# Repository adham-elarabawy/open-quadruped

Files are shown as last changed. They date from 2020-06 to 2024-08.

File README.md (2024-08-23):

# open-quadruped

PR (https://github.com/adham-elarabawy/OpenQuadruped/pulls)



An open-source 3D-printed quadrupedal robot. Intuitive gait generation through 12-DOF Bezier Curves. Full 6-axis body pose manipulation. Custom 3DOF Leg Inverse Kinematics Model accounting for offsets.

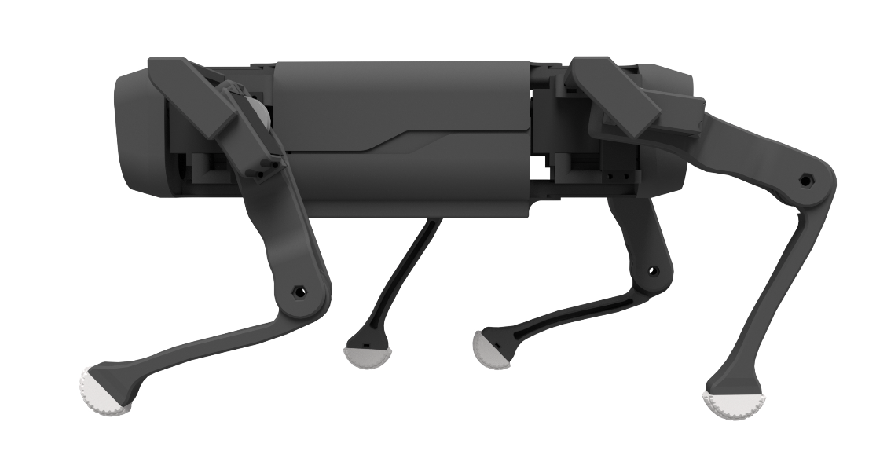
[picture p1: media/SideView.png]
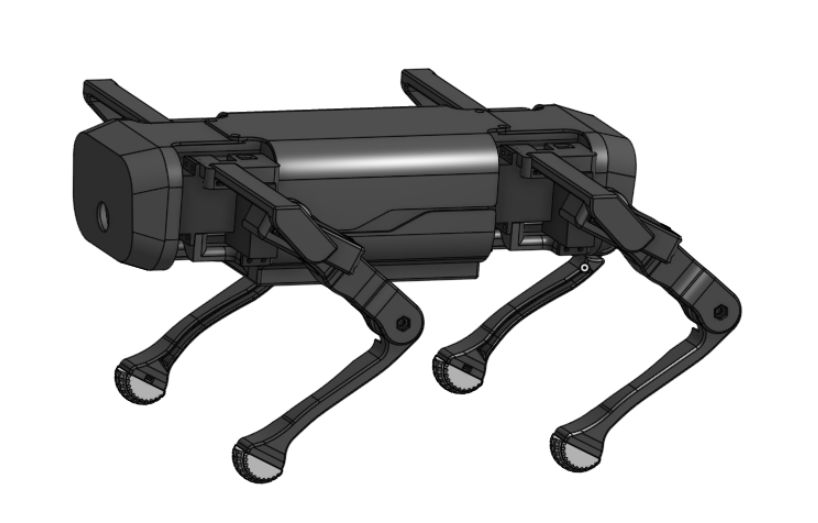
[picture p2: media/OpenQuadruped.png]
 

## Current Status
### To-Do List

- [x] *Hardware* // Redesign legs to move actuators closer to hip + reinforce all servo mounting.
- [ ] *Design* // Research transition between gait & body pose.
- [x] *Software* // Implementing ROS infrastructure for all control processes (including cpp on teensy).
- [ ] *Software* // Write & automate pytest unit tests.
- [ ] *Software* // Integrate unit tests with github actions.
- [x] *Simulation* // Create URDF model. (or port collaborater's URDF: Maurice Rahme)
- [x] *Simulation* // Gazebo
- [ ] *Simulation* // RViz Realtime Model
- [ ] *Design* // Solve offset 3DOF IK model for right limbs _OR_ validate that mirroring angles works for left/right legs
- [ ] *Simulation* // Implement WebGazebo clientside support for non-linux users
- [ ] *Sim-to-Real* // Joint servo calibration
- [ ] *Sim-to-Real* // Refining gait parameters
- [ ] *Simulation* // Reinforcement learning via ARS
- [ ] *Software* // Raibert Huerestic for converting desired velocities into gait parameters
- [ ] *Software* // ROS Nav Stack Layer

  

## Papers
I've been formally documenting this project in the form of papers. You can find them here: [adhamelarabawy.com/images/IK_Model.pdf](https://www.adhamelarabawy.com/images/IK_Model.pdf)

## Documentation
You can find a summary of this project on [my portfolio website's project page](https://www.adhamelarabawy.com).
I'm hosting most of the technical documentation for this project on [this repo's wiki](https://github.com/adham-elarabawy/OpenQuadruped/wiki).

## 3D Model
In the [model](https://github.com/adham-elarabawy/OpenQuadruped/tree/master/model) folder, you can find all of the step & stl files that I used for my build of OpenQuadruped. There, you can also find a Bill of Materials, and some guides (in progress). 

## Hardware
I made a custom pcb board to control the position and speed of 12 servos simultaneously, as well as interface with all of the sensors.

You can find the gerber files for the custom pcb in the [hardware folder](https://github.com/adham-elarabawy/OpenQuadruped/tree/master/hardware) in this repository.

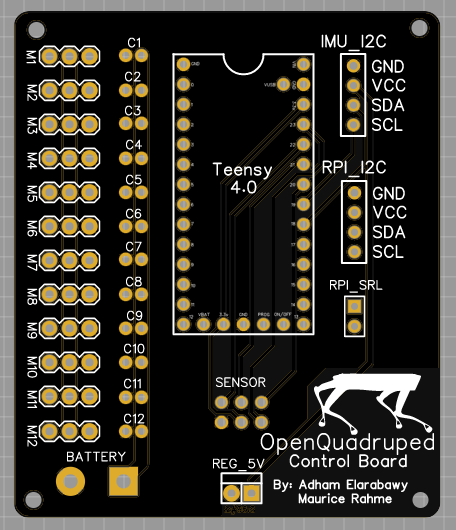
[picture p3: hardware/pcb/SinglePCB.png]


You can find the bill of materials for this project [here](https://docs.google.com/spreadsheets/d/12QX1ca9LHZEThukprlz0DARR9_lmf6FJI8Tg-O4qcdc/edit?usp=sharing).

## Visualization Usage
*NOTE: There are 3 different visualization tools: Gazebo Simulator (ROS + Physics), RViz (ROS), & my custom 3d-matplotlib visualization tool (body IK model + leg IK model). The latter tool is still under development, and I haven't ported it to use my new control library yet, so it is likely broken for the time being.*

To try the visualization tool out, you'll need to run the [animate.py](https://github.com/adham-elarabawy/OpenQuadruped/blob/master/visualization/animate.py) python file with the proper libraries installed. (matplotlib 3.0.3 supported).

You can then use keyboard controls: use x, y, z, a, p, r to select (x axis, y axis, z axis, yaw, pitch, roll), and then the up and down buttons to increment the selected position. If you click '1' on your keyboard, it will reset the position. 

Right now, if you try to go to an impossible pose that would result in collisions, the body will do some weird things. If that happens, just click "1" on your keyboard to reset the position. 

*Note: Pitch and Roll are currently not working. I am currently trying to fix that.*

## More Demos
Force Sensitive Leg Test (https://www.youtube.com/watch?v=z8j-Z9Bwn58)IK Model Demo 0 (https://www.youtube.com/watch?v=79kFujIpjgo)IK Model Demo 1 (https://www.youtube.com/watch?v=cCMvCH0m9TA)IK Model Visualization (https://www.youtube.com/watch?v=LBjqJVEXwhM)

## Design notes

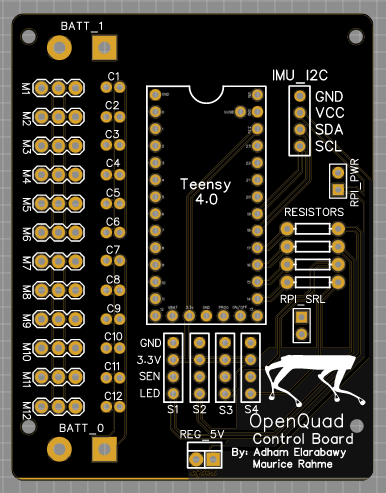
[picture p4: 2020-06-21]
hardware/pcb/DoublePCB.png

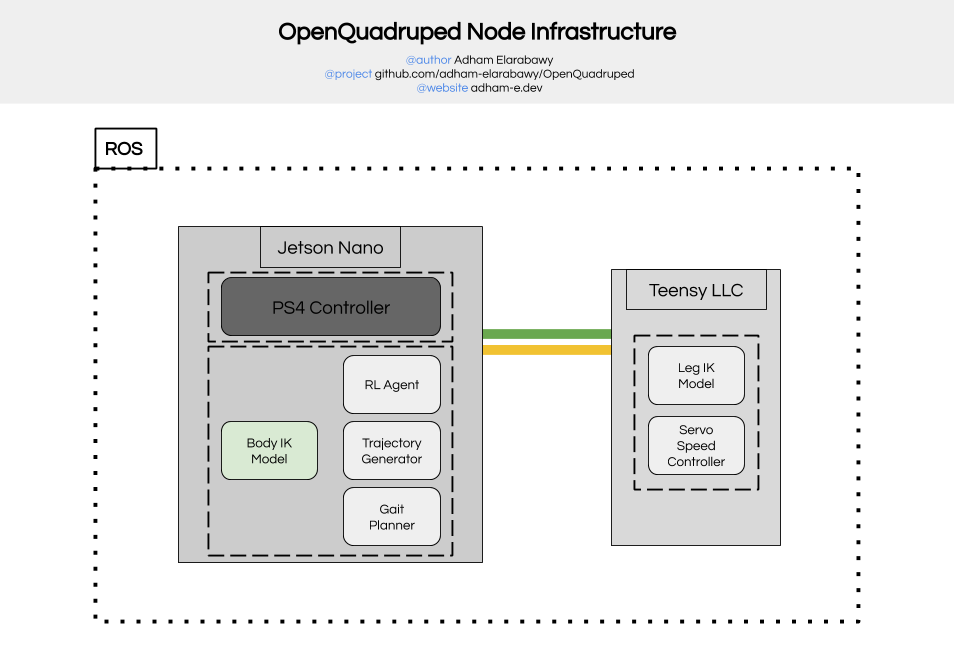
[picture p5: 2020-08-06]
media/OpenQuadruped Node Infrastructure.png

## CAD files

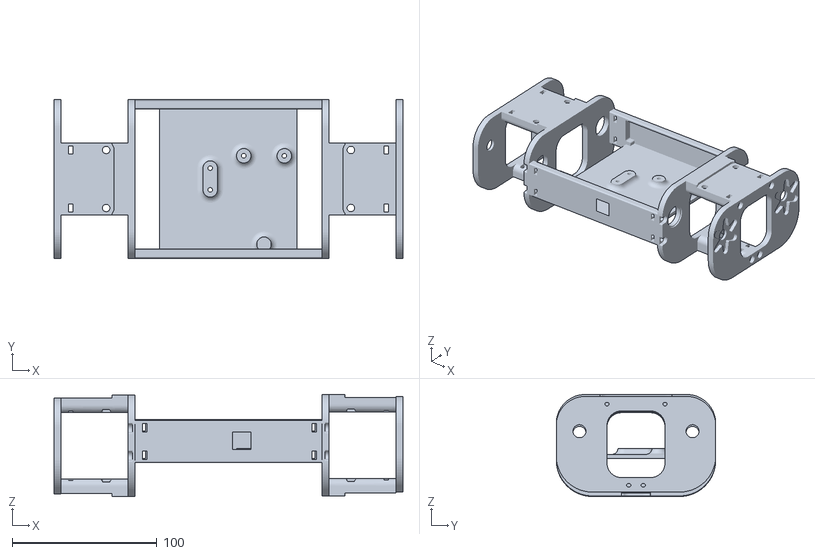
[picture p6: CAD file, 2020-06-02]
ros-workspace/src/open_quadruped/urdf/stl/mainbody.stl
240.7 x 110.0 x 70.4

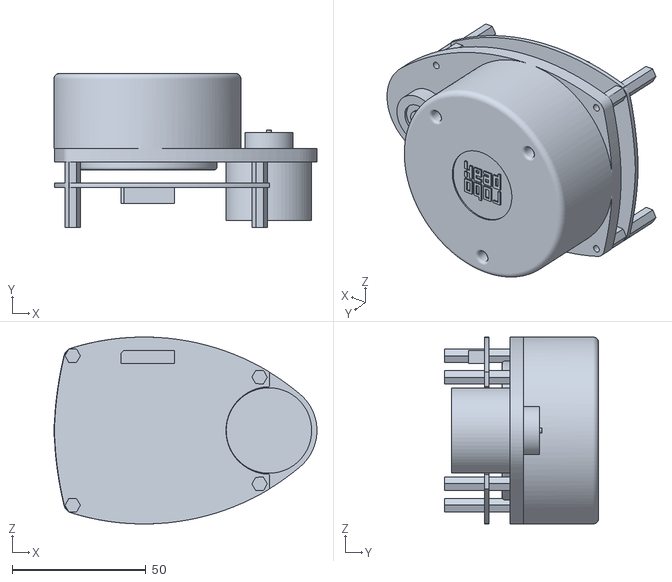
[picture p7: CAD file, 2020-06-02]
ros-workspace/src/open_quadruped/urdf/stl/rplidar_main.stl
98.5 x 57.7 x 70.0

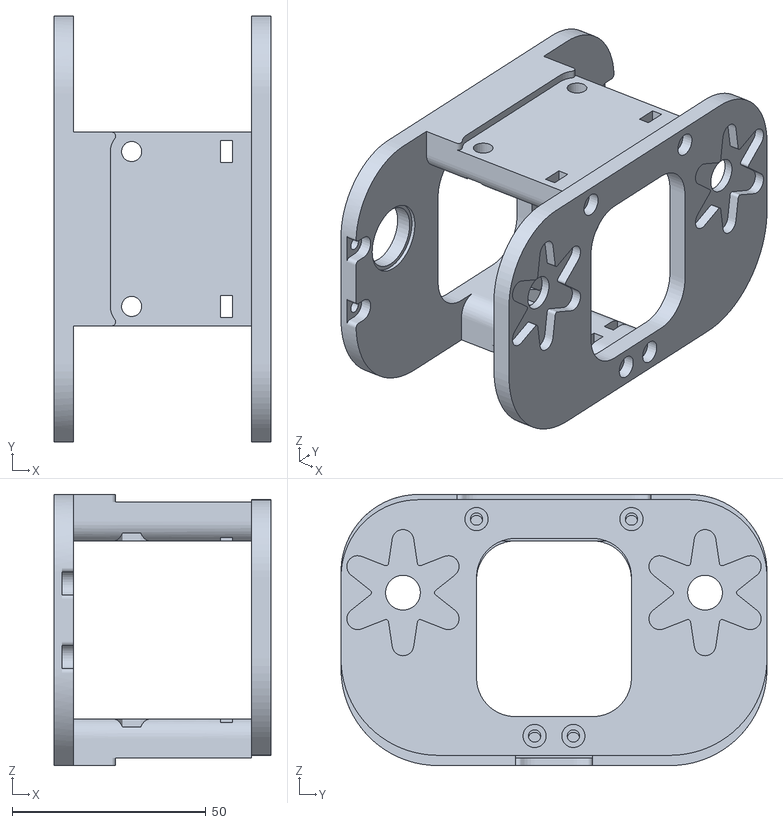
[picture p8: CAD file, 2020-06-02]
ros-workspace/src/open_quadruped/urdf/stl/rearmain.stl
55.9 x 110.0 x 70.0

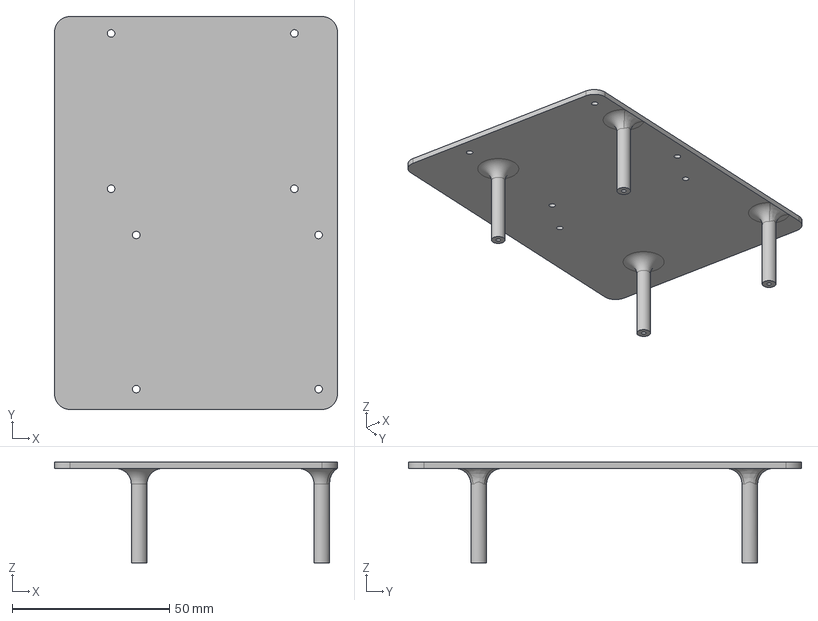
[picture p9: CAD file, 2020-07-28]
hardware/3d-printing/Body/step/Adapter_Plate.step
90.0 x 125.0 x 32.0 mm

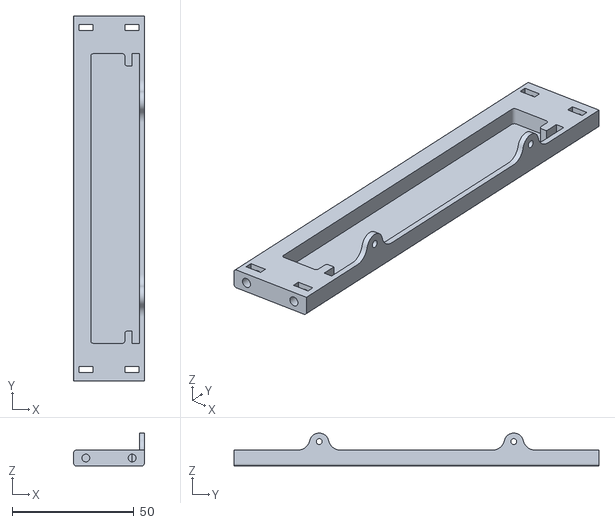
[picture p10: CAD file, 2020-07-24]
hardware/3d-printing/Body/stl/Chassis_Right_Side.stl
29.0 x 150.0 x 13.5

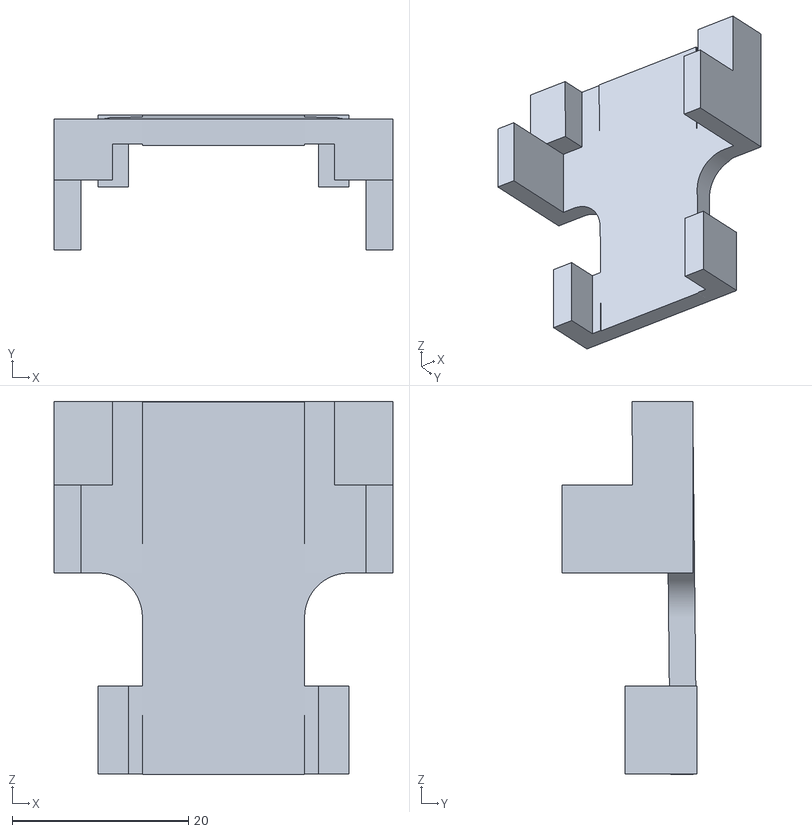
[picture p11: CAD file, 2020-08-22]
hardware/3d-printing/Calibration/Lower_Leg_Calibrator.stl
38.4 x 15.2 x 42.3

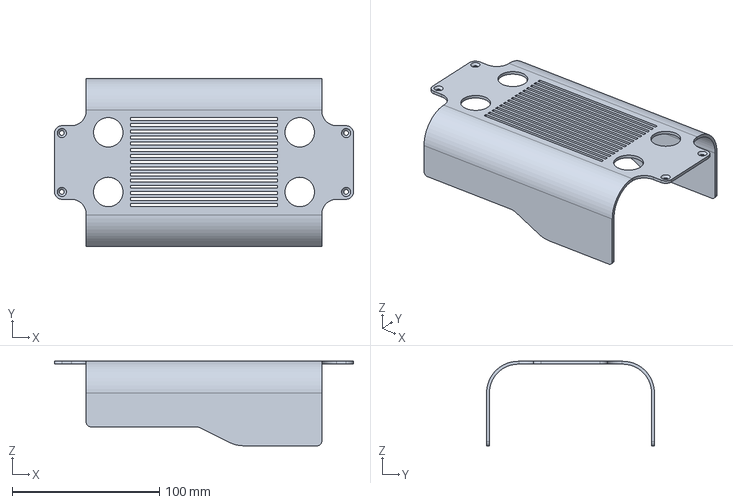
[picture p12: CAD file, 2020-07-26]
hardware/3d-printing/Covers/step/Top.step
203.0 x 114.0 x 57.4 mm

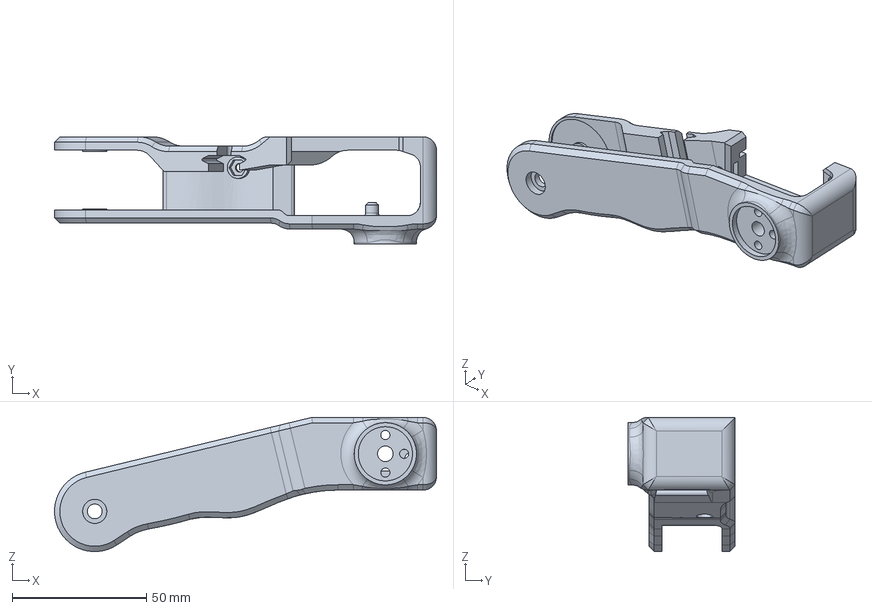
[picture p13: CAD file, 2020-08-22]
hardware/3d-printing/Legs/Left/step/Upper_Leg.step
142.3 x 40.0 x 50.0 mm

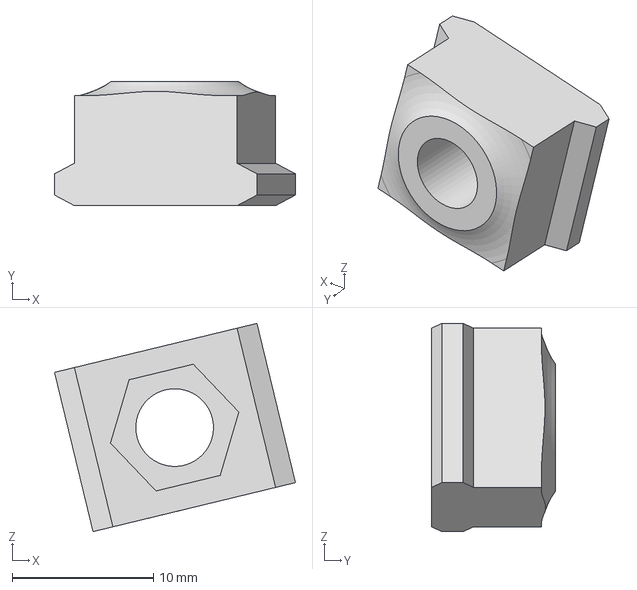
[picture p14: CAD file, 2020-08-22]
hardware/3d-printing/Legs/Right/step/Idler_Mount.step
17.1 x 8.80 x 14.7 mm

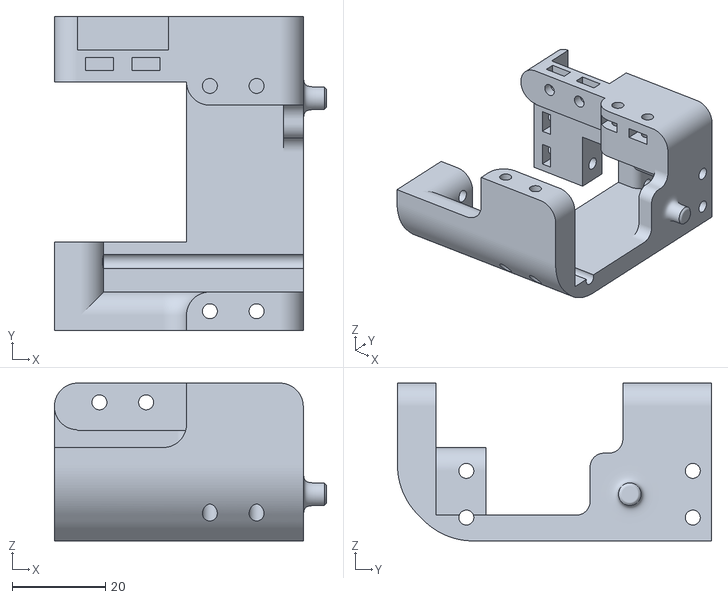
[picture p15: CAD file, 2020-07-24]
model/Legs/Left/stl/Left_Hip_Joint.stl
58.3 x 67.2 x 33.8

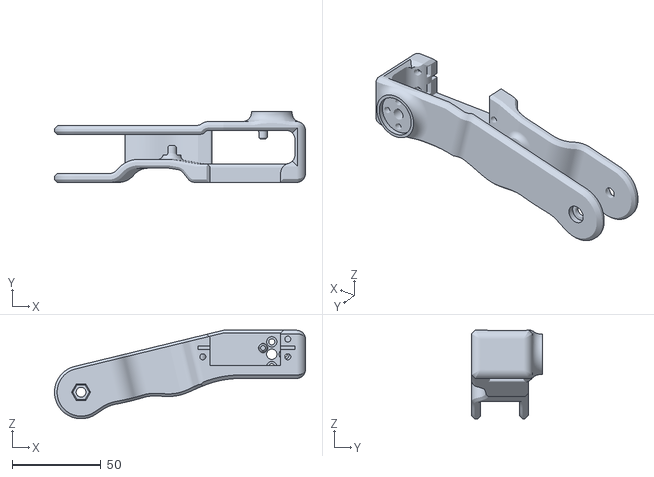
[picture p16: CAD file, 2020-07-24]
model/Legs/Right/stl/Upper_Leg.stl
141.8 x 40.0 x 50.0

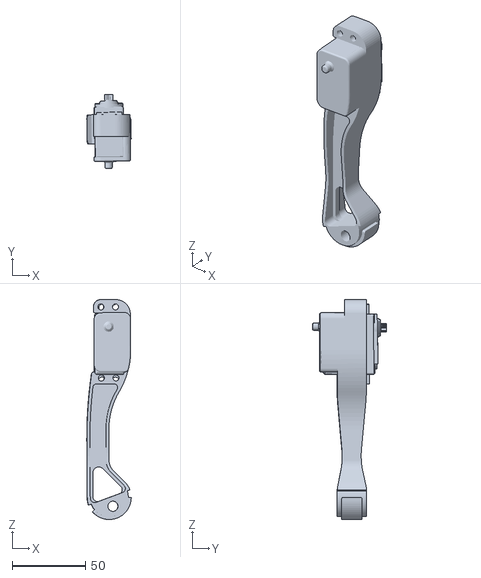
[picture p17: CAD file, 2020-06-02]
ros-workspace/src/open_quadruped/urdf/stl/lfoot.stl
30.4 x 50.7 x 150.0

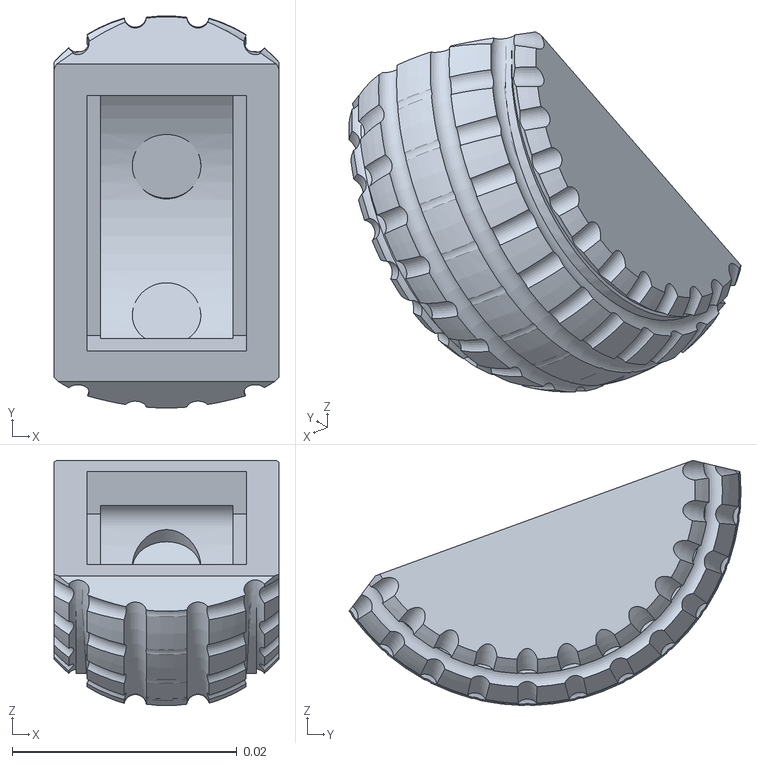
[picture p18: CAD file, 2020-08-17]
ros-workspace/src/open_quadruped/urdf/stl/OpenQuadruped/RIGHT_FOOT.stl
0.02 x 0.0349 x 0.0218

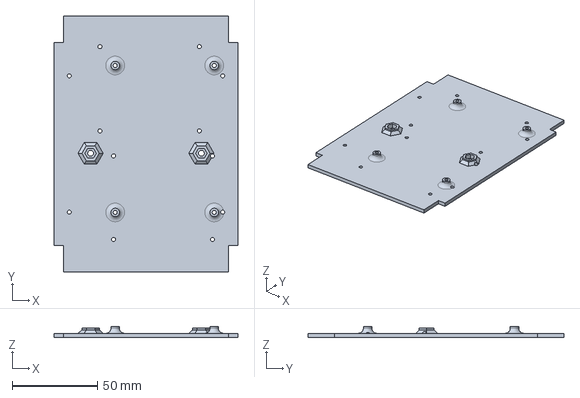
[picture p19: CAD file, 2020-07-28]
hardware/3d-printing/Body/step/Electronics_Plate.step
108.0 x 149.9 x 6.50 mm

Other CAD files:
hardware/3d-printing/Calibration/Hip_Calibrator.stl
hardware/3d-printing/Covers/step/Rear.step
hardware/3d-printing/Legs/Left/step/Idler_Mount.step
hardware/3d-printing/Legs/Right/step/Upper_Leg.step
hardware/3d-printing/Body/step/Back_Inner_Shoulder.step
hardware/3d-printing/Body/step/Back_Outer_Shoulder.step
hardware/3d-printing/Body/step/Chassis_Left_Side - Chassis_Right_Side.step
hardware/3d-printing/Body/step/Chassis_Left_Side.step
hardware/3d-printing/Body/step/Front_Inner_Shoulder.step
hardware/3d-printing/Body/step/Front_Outer_Shoulder.step
hardware/3d-printing/Body/stl/Adapter_Plate.stl
hardware/3d-printing/Body/stl/Back_Inner_Shoulder.stl
hardware/3d-printing/Body/stl/Back_Outer_Shoulder.stl
hardware/3d-printing/Body/stl/Electronics_Plate.stl
hardware/3d-printing/Body/stl/Front_Inner_Shoulder.stl
hardware/3d-printing/Body/stl/Front_Outer_Shoulder.stl
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

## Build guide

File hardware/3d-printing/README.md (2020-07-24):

# 3D Model
In this folder, you can find all of the modified step & stl files that I used for my build of OpenQuadruped.

## Instructions
In Progress...

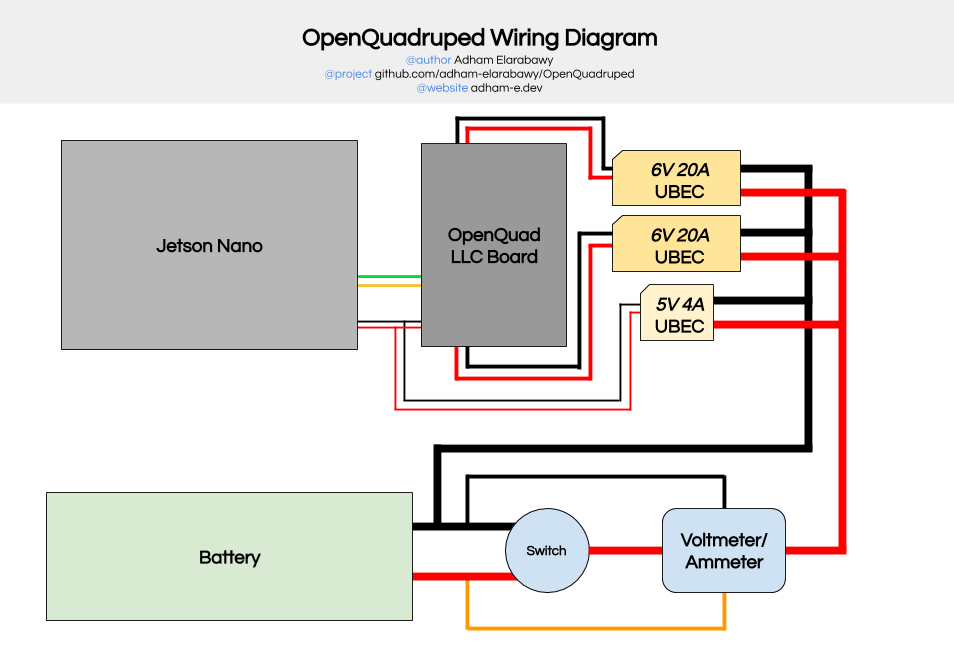
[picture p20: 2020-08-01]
media/wiring_diagram.png

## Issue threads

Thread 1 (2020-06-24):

Servo Detach() function

mano1979, 2020-06-24:
I wondered if you could add a function like this to the servo control code. It is to detach the servos and thus make them loose power. This is handy for shutting the robot down in an emergency for example. i am not familiar enough with your code yet so i can not implement it myself.

Here is the piece of code from the normal arduino Servo.cpp:

`void Servo::detach()
{
  servos[this->servoIndex].Pin.isActive = false;
  timer16_Sequence_t timer = SERVO_INDEX_TO_TIMER(servoIndex);
  if(isTimerActive(timer) == false) {
    finISR(timer);
  }
}`

adham-elarabawy, 2020-06-24:
Great Idea! I will put this on the to-do list.

mano1979, 2020-06-25:
Also, is this teensy code complete? I cannot find any pin definitions anywhere. Where do you tell it to use the GPIO 2-12 for the servos?

adham-elarabawy, 2020-06-30:
I haven't properly documented everything yet. The plan is to do that sometime this week.

I tried to servo.detach() that you mentioned, but it doesn't really release the servos in the way that I expected. Most servos hold their positions when you detach them, not actually release servo power. This behavior is equivalent to my estop functionality on the teensy, which halts all the servos as soon as 'e' or 'E' is sent over serial, so I think servo.detach is redundant.

mano1979, 2020-07-07:
I found this topic online that explains why it doesn't work and a possible workaround. it seems the timers on the teensy aren't reset when a servo is detached, keeping the PWM signal alive ( if i understood right).

https://github.com/arduino/Arduino/issues/3860

adham-elarabawy, 2020-07-11:
I'll take a look.

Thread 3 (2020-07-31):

Integrating with ROS

adham-elarabawy, 2020-07-31:
In order to switch to using a ROS infrastructure, there needs to be significant work done on refactoring much of the codebase. It is as follows:
 - [x] Jetson Nano Networking setup
   - [x] autoconnect to laptop's network
   - [x] document connection procedure
 - [x] Install ROS melodic on Jetson Nano
 - [ ] Verify ROS functionality
   - [x] sub & pub to topics using nodes on jetson nano
   - [x] serial comm between jetson nano / teensy
   - [x] sub & pub to topics using nodes on jetson nano / teensy
   - [ ] ~sub & pub to topics using nodes on teensy~
     - Not possible. Teensy can only act as 1 node.
 - [x] Based on the results of above task, determine proper node layout
   - [x] create diagram (https://github.com/adham-elarabawy/OpenQuadruped/wiki/ROS-Node-Infrastructure)
 - [ ] Refactor codebase
   - [x] Import ros libs in teensy lib dir
   - [x] Implement base ROS init + callback in teensy
   - [x] Test ros joy lib with ds4drv ps4 driver
   - [x] Create custom message for 4 leg poses
   - [x] Header files for custom message on teensy
   - [x] Experiment with ROS ps4 controller packages
   - [x] Minor refactoring for main jetson nano control process. Node-ify it.
   - [ ] Modify LLC c++ code to remove Leg IK from teensy (LLC should accept joint angles, not leg htf vectors).

adham-elarabawy, 2020-08-01:
All references to "documentation" are referring to the repo wiki.

caelinsutch, 2020-08-06:
Are you planning on integrating sim?

adham-elarabawy, 2020-08-06:
Yes, but I'm not sure if I'm going to use Gazebo or pybullet

adham-elarabawy, 2020-08-06:
I'd like to finish base ROS integration first, then write some unit tests for some of the inverse kinematics classes. Then, sim -> RL.

adham-elarabawy, 2020-08-06:
Created ROS Node Infrastructure diagram + explanation of control processes. https://github.com/adham-elarabawy/OpenQuadruped/wiki/ROS-Node-Infrastructure

caelinsutch, 2020-08-06:
> Created ROS Node Infrastructure diagram + explanation of control processes. https://github.com/adham-elarabawy/OpenQuadruped/wiki/ROS-Node-Infrastructure

You didn't link anything

adham-elarabawy, 2020-08-06:
> > Created ROS Node Infrastructure diagram + explanation of control processes. https://github.com/adham-elarabawy/OpenQuadruped/wiki/ROS-Node-Infrastructure
>
> You didn't link anything

Hm, on my end it looks like I linked the documentation in the comment you replied to + in the checklist. Is that not showing up for you?

caelinsutch, 2020-08-06:
@adham-elarabawy Mobile redirected me to the home page, on my desktop it's showing up fine!

caelinsutch, 2020-08-19:
The package configuration is still pretty non standard, take a look at [this repo](https://github.com/chvmp/champ)

Closed 2020-08-17.

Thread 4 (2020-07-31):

Inverse Kinematics Model revision

adham-elarabawy, 2020-07-31:
After using the IK model I created & documented, I have noticed some flaws with my implementation. I'd like to try out a couple of new things:
 - [ ] Error catching
   - [ ] Out of bounds
   - [ ] Ability to set custom limits on arm angles based on hardware restrictions
 - [ ] Use right hand rule model consistently
 - [ ] Update documentation

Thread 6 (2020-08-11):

About the pulleys on the 3D model

takanotume24, 2020-08-11:
Hi, I'm from the spot_mini_mini repository.
I saw the video on Youtube, and I think it's a great robot, so I'd love to make one myself!

Viewed on https://cad.onshape.com/documents/9d0f96878c54300abf1157ac/w/c9cdf8daa98d8a0d7d50c8d3/e/fa0d7caf0ed2ef46834ecc24, Did you make the pulleys with a 3D printer?
Or do you use a commercial product?

adham-elarabawy, 2020-08-11:
The pulleys (like 90% of the parts on the quadruped) are 3D printed. They're made to fit 300mm 2GT belts. Please let me know if you have any other questions.

Closed 2020-08-11.

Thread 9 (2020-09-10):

Assembly specifically belt tensioner

wiltonburke, 2020-09-10:
Do you have any documents or guides on assembly. I'm not sure exactly how you did the belt tension. Also the alignment of the servos would also be helpful. If not guides them possibly some pictures.

Thank You.

wiltonburke, 2020-09-10:
This is what I have so far. It looks like it would bind or wear out poorly against the side of leg.

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

adham-elarabawy, 2020-09-10:
Hi @wiltonburke. I'm currently a bit busy with my undergraduate workload, but I can try and guide you through the assembly. From the picture, it looks like the belt is slipped off of the bearing. The ideal behavior is that the belt lies flat against the idler bearing. Please try reorienting it and let me know if that solves your problem.

wiltonburke, 2020-09-10:
I may adjust the design to use something like https://www.thingiverse.com/thing:24661

On the alignment of the servos I can see it doesn't matter much on the belt thats pretty adjustable to fix by sliding the belt. But the alignment on the 2 shoulder servos. What do you recommend?

adham-elarabawy, 2020-09-11:
By alignment of the shoulder servos, do you mean the range of the servo? Or are you referencing mechanical alignment? There should only be one way to mount the shoulder servos.

wiltonburke, 2020-09-11:
I mean the range of the servos. Where do you place the min and the max. The servos usually provide 180 degrees of motion. I don't know how much experimentation you have done, but I'm asking because I noticed when I put the leg together the first time I placed it where it would have very little motion stepping forward. The 2 servos in the shoulder are a little harder to adjust then the belt drive to the lower leg so I'd like to get them aligned correctly before building the other 3 legs. I'll have to rebuild the first leg anyways because I order some 35kg servos to replace the mixture I have now.

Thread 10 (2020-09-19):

initial pose at boot needed for servos placement !!

elpimous, 2020-09-19:
Hey, Adham, working on your package, and need to know what alignement servos need to be at teensy boot !!
Could you quickly tell me their position :
- Hips right, and parallel to ground ?
- shoulders // to others shoulders, and perpendicular to ground ?
- wrist        // to others wrists, and perpendicular to ground ?
Thanks in avance, Adham
Vincent

domcross, 2021-01-02:
There is a calibration mode that sets servos to aligned positions, see calibration guide for details: https://github.com/OpenQuadruped/spot_mini_mini/blob/spot/spot_real/Calibration.md

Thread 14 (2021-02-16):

Parts list link no longer working

ARingshall, 2021-02-16:
Hi Adham
great project, just wondering if you have the parts list still available as it appears to have been deleted?

Cheers
Alex

domcross, 2021-02-17:
see link "BOM" here: https://github.com/OpenQuadruped/spot_mini_mini/tree/spot/spot_real

or direct link: https://docs.google.com/spreadsheets/d/1Z4y59K8bY3r_442I70xe564zAFuP0pVIFEJ6bNZaCi0/edit?usp=sharing

ARingshall, 2021-02-19:
Nice one, cheers mate

Closed 2021-02-19.

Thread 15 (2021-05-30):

Idler stl missing

rachaelsmith423, 2021-05-30:
I see in both the leg folders, there is a idler mount stl. I also see in the CAD model that there is an idler. Yet, I don't see where the actual idler's stl file. Would you please mind uploading this? I assembled the rest, but tensioning the belt would definitely make the legs move better. Thank you

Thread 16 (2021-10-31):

Broken bill of materials link - says that the file was deleted

Milind220, 2021-10-31:

domcross, 2021-10-31:
The link to the BOM was most likely deleted because Adhams repo is outdated - I would recommend to use the new repo instead:
https://github.com/OpenQuadruped/spot_mini_mini

Link to latest BOM can be found there as well (in section [spot_real](https://github.com/OpenQuadruped/spot_mini_mini/tree/spot/spot_real)): https://docs.google.com/spreadsheets/d/1Z4y59K8bY3r_442I70xe564zAFuP0pVIFEJ6bNZaCi0/edit?usp=sharing

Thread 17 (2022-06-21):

animate.py roll pitch yaw

haxord7hasib, 2022-06-21:
roll pitch way is not working on animate.py. Is there any update available?

Closed 2022-06-21.

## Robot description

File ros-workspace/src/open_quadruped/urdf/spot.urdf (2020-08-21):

<?xml version="1.0" encoding="utf-8"?>
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
<robot name="spot">
  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
  <link name="base_link"/>
  <link name="base_inertia">
    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
    <inertial>
      <mass value="0.6"/>
      <origin rpy="0 0 0" xyz="0 0 0"/>
      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
    </inertial>
  </link>
  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
  <link name="battery">
    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
    <inertial>
      <mass value="0.4"/>
      <origin rpy="0 0 0" xyz="0 0 0"/>
      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
    </inertial>
  </link>
  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
  <link name="chassis_left">
    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
    <inertial>
      <mass value="0.01"/>
      <origin rpy="0 0 0" xyz="0 0 0"/>
      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
    </inertial>
  </link>
  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
  <link name="chassis_right">
    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
    <inertial>
      <mass value="0.01"/>
      <origin rpy="0 0 0" xyz="0 0 0"/>
      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
    </inertial>
  </link>
  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
  <link name="front">
    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
    <inertial>
      <mass value="0.1"/>
      <origin rpy="0 0 0" xyz="0 0 0"/>
      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
    </inertial>
  </link>
  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
  <link name="back">
    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
    <inertial>
      <mass value="0.1"/>
      <origin rpy="0 0 0" xyz="0 0 0"/>
      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
    </inertial>
  </link>
  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
  <link name="front_bracket">
    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
    <inertial>
      <mass value="0.1"/>
      <origin rpy="0 0 0" xyz="0 0 0"/>
      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
    </inertial>
  </link>
  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
  <link name="back_bracket">
    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
    <inertial>
      <mass value="0.1"/>
      <origin rpy="0 0 0" xyz="0 0 0"/>
      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
    </inertial>
  </link>
  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
  <link name="front_left_hip">
    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
    <inertial>
      <mass value="0.2"/>
      <origin rpy="0 0 0" xyz="0 0.075 0"/>
      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
    </inertial>
  </link>
  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
  <joint name="motor_front_left_hip" type="revolute">
    <axis xyz="1 0 0"/>
    <origin rpy="0 0 0" xyz="0.0915 0.0394 0.022"/>
    <parent link="front_bracket"/>
    <child link="front_left_hip"/>
    <limit effort="4.0" lower="-1.04" upper="1.04" velocity="4.0"/>
    <joint_properties damping="0.0" friction="0.0"/>
  </joint>
  <link name="front_left_upper_leg">
    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
    <inertial>
      <mass value="0.13"/>
      <origin rpy="0 0 0" xyz="-0.005 0.0175 -0.055"/>
      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
    </inertial>
  </link>
  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
  <joint name="motor_front_left_upper_leg" type="revolute">
    <axis xyz="0 1 0"/>
    <origin rpy="0 0 0" xyz="0.0015 0.045 -0.0087"/>
    <parent link="front_left_hip"/>
    <child link="front_left_upper_leg"/>
    <limit effort="4.0" lower="-1.57079632679" upper="2.59" velocity="4.0"/>
    <joint_properties damping="0.0" friction="0.0"/>
  </joint>
  <link name="front_left_lower_leg">
    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
    <inertial>
      <mass value="0.05"/>
      <origin rpy="0 0 0" xyz="-0.01 0 -0.06"/>
      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
    </inertial>
  </link>
  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
  <joint name="motor_front_left_lower_leg" type="revolute">
    <axis xyz="0 1 0"/>
    <origin rpy="0 0 0" xyz="-0.005 0.018 -0.109"/>
    <parent link="front_left_upper_leg"/>
    <child link="front_left_lower_leg"/>
    <limit effort="4.0" lower="-2.9" upper="1.57079632679" velocity="4.0"/>
    <joint_properties damping="0.0" friction="0.0"/>
  </joint>
  <link name="front_left_foot">
    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
    <inertial>
      <mass value="0.005"/>
      <origin rpy="0 0 0" xyz="0 0 0"/>
      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
    </inertial>
  </link>
  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
  <joint name="front_left_leg_foot" type="fixed">
    <origin rpy="0 0 0" xyz="0 0 -0.1265"/>
    <parent link="front_left_lower_leg"/>
    <child link="front_left_foot"/>
  </joint>
  <link name="back_left_hip">
    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
    <inertial>
      <mass value="0.2"/>
      <origin rpy="0 0 0" xyz="0 0.075 0"/>
      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
    </inertial>
  </link>
  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
  <joint name="motor_back_left_hip" type="revolute">
    <axis xyz="1 0 0"/>
    <origin rpy="0 0 0" xyz="-0.1365 0.0394 0.022"/>
    <parent link="back_bracket"/>
    <child link="back_left_hip"/>
    <limit effort="4.0" lower="-1.04" upper="1.04" velocity="4.0"/>
    <joint_properties damping="0.0" friction="0.0"/>
  </joint>
  <link name="back_left_upper_leg">
    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
    <inertial>
      <mass value="0.13"/>
      <origin rpy="0 0 0" xyz="-0.005 0.0175 -0.055"/>
      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
    </inertial>
  </link>
  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
  <joint name="motor_back_left_upper_leg" type="revolute">
    <axis xyz="0 1 0"/>
    <origin rpy="0 0 0" xyz="0.0015 0.045 -0.0087"/>
    <parent link="back_left_hip"/>
    <child link="back_left_upper_leg"/>
    <limit effort="4.0" lower="-1.57079632679" upper="2.59" velocity="4.0"/>
    <joint_properties damping="0.0" friction="0.0"/>
  </joint>
  <link name="back_left_lower_leg">
    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
    <inertial>
      <mass value="0.05"/>
      <origin rpy="0 0 0" xyz="-0.01 0 -0.06"/>
      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
    </inertial>
  </link>
  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
  <joint name="motor_back_left_lower_leg" type="revolute">
    <axis xyz="0 1 0"/>
    <origin rpy="0 0 0" xyz="-0.005 0.018 -0.109"/>
    <parent link="back_left_upper_leg"/>
    <child link="back_left_lower_leg"/>
    <limit effort="4.0" lower="-2.9" upper="1.57079632679" velocity="4.0"/>
    <joint_properties damping="0.0" friction="0.0"/>
  </joint>
  <link name="back_left_foot">
    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
    <inertial>
      <mass value="0.005"/>
      <origin rpy="0 0 0" xyz="0 0 0"/>
      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
    </inertial>
  </link>
  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
  <joint name="back_left_leg_foot" type="fixed">
    <origin rpy="0 0 0" xyz="0 0 -0.1265"/>
    <parent link="back_left_lower_leg"/>
    <child link="back_left_foot"/>
  </joint>
  <link name="front_right_hip">
    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
    <inertial>
      <mass value="0.2"/>
      <origin rpy="0 0 0" xyz="0 -0.075 0"/>
      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
    </inertial>
  </link>
  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
  <joint name="motor_front_right_hip" type="revolute">
    <axis xyz="1 0 0"/>
    <origin rpy="0 0 0" xyz="0.0915 -0.0394 0.022"/>
    <parent link="front_bracket"/>
    <child link="front_right_hip"/>
    <limit effort="4.0" lower="-1.04" upper="1.04" velocity="4.0"/>
    <joint_properties damping="0.0" friction="0.0"/>
  </joint>
  <link name="front_right_upper_leg">
    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
    <inertial>
      <mass value="0.13"/>
      <origin rpy="0 0 0" xyz="-0.005 -0.0175 -0.055"/>
      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
    </inertial>
  </link>
  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
  <joint name="motor_front_right_upper_leg" type="revolute">
    <axis xyz="0 1 0"/>
    <origin rpy="0 0 0" xyz="0.0015 -0.045 -0.0087"/>
    <parent link="front_right_hip"/>
    <child link="front_right_upper_leg"/>
    <limit effort="4.0" lower="-1.57079632679" upper="2.59" velocity="4.0"/>
    <joint_properties damping="0.0" friction="0.0"/>
  </joint>
  <link name="front_right_lower_leg">
    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
    <inertial>
      <mass value="0.05"/>
      <origin rpy="0 0 0" xyz="-0.01 0 -0.06"/>
      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
    </inertial>
  </link>
  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
  <joint name="motor_front_right_lower_leg" type="revolute">
    <axis xyz="0 1 0"/>
    <origin rpy="0 0 0" xyz="-0.005 -0.018 -0.109"/>
    <parent link="front_right_upper_leg"/>
    <child link="front_right_lower_leg"/>
    <limit effort="4.0" lower="-2.9" upper="1.57079632679" velocity="4.0"/>
    <joint_properties damping="0.0" friction="0.0"/>
  </joint>
  <link name="front_right_foot">
    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
    <inertial>
      <mass value="0.005"/>
      <origin rpy="0 0 0" xyz="0 0 0"/>
      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
    </inertial>
  </link>
  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
  <joint name="front_right_leg_foot" type="fixed">
    <origin rpy="0 0 0" xyz="0 0 -0.1265"/>
    <parent link="front_right_lower_leg"/>
    <child link="front_right_foot"/>
  </joint>
  <link name="back_right_hip">
    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
    <inertial>
      <mass value="0.2"/>
      <origin rpy="0 0 0" xyz="0 -0.075 0"/>
      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
    </inertial>
  </link>
  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
  <joint name="motor_back_right_hip" type="revolute">
    <axis xyz="1 0 0"/>
    <origin rpy="0 0 0" xyz="-0.1365 -0.0394 0.022"/>
    <parent link="back_bracket"/>
    <child link="back_right_hip"/>
    <limit effort="4.0" lower="-1.04" upper="1.04" velocity="4.0"/>
    <joint_properties damping="0.0" friction="0.0"/>
  </joint>
  <link name="back_right_upper_leg">
    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
    <inertial>
      <mass value="0.13"/>
      <origin rpy="0 0 0" xyz="-0.005 -0.0175 -0.055"/>
      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
    </inertial>
  </link>
  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
  <joint name="motor_back_right_upper_leg" type="revolute">
    <axis xyz="0 1 0"/>
    <origin rpy="0 0 0" xyz="0.0015 -0.045 -0.0087"/>
    <parent link="back_right_hip"/>
    <child link="back_right_upper_leg"/>
    <limit effort="4.0" lower="-1.57079632679" upper="2.59" velocity="4.0"/>
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

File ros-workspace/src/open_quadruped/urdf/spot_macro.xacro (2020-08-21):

<?xml version="1.0" ?>
<robot xmlns:xacro="http://www.ros.org/wiki/xacro">

  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

  <xacro:macro name="rev_joint" params="name type axis_xyz origin_rpy origin_xyz parent child effort velocity damping friction upper lower">
    <joint name="${name}" type="${type}">
      <axis xyz="${axis_xyz}" />
      <origin rpy="${origin_rpy}" xyz="${origin_xyz}" />
      <parent link="${parent}" />
      <child link="${child}" />
      <limit effort="${effort}" velocity="${velocity}" lower="${lower}" upper="${upper}"/>
      <joint_properties damping="${damping}" friction="${friction}" />
    </joint>
  </xacro:macro>

  <xacro:macro name="frame_joint" params="name type origin_rpy origin_xyz parent child">
    <joint name="${name}" type="${type}">
      <origin rpy="${origin_rpy}" xyz="${origin_xyz}" />
      <parent link="${parent}" />
      <child link="${child}" />
    </joint>
  </xacro:macro>

  <xacro:macro name="mesh_link" params="name origin_xyz origin_rpy meshfile meshscale c_xyz matname mass i_xyz i_rpy length width height">
    <link name="${name}">
      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

      <inertial>
        <mass value="${mass}" />
        <origin rpy="${i_rpy}" xyz="${i_xyz}" /> 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
      </inertial>
    </link>
    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
  </xacro:macro>

  <xacro:macro name="mesh_link_sphere" params="name origin_xyz origin_rpy meshfile meshscale c_xyz matname mass i_xyz i_rpy length width height radius">
    <link name="${name}">
      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

      <inertial>
        <mass value="${mass}" />
        <origin rpy="${i_rpy}" xyz="${i_xyz}" /> 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
      </inertial>
    </link>

    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
  </xacro:macro>


  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

</robot>

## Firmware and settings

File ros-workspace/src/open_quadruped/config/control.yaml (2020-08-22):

plen:
  # Publish all joint states -----------------------------------
  joint_state_controller:
    type: joint_state_controller/JointStateController
    publish_rate: 50

  # Position Controllers ---------------------------------------
  j1_pc:
    type: effort_controllers/JointPositionController
    joint: motor_front_left_shoulder
    pid: {p: 4.0, i: 0.001, d: 0.0023}
  j2_pc:
    type: effort_controllers/JointPositionController
    joint: motor_front_left_leg
    pid: {p: 4.0, i: 0.001, d: 0.0023}
  j3_pc:
    type: effort_controllers/JointPositionController
    joint: foot_motor_front_left
    pid: {p: 4.0, i: 0.001, d: 0.0023}
  j4_pc:
    type: effort_controllers/JointPositionController
    joint: motor_front_right_shoulder
    pid: {p: 4.0, i: 0.001, d: 0.0023}
  j5_pc:
    type: effort_controllers/JointPositionController
    joint: motor_front_right_leg
    pid: {p: 4.0, i: 0.001, d: 0.0023}
  j6_pc:
    type: effort_controllers/JointPositionController
    joint: foot_motor_front_right
    pid: {p: 4.0, i: 0.001, d: 0.0023}
  j7_pc:
    type: effort_controllers/JointPositionController
    joint: motor_rear_left_shoulder
    pid: {p: 4.0, i: 0.001, d: 0.0023}
  j8_pc:
    type: effort_controllers/JointPositionController
    joint: motor_rear_left_leg
    pid: {p: 4.0, i: 0.001, d: 0.0023}
  j9_pc:
    type: effort_controllers/JointPositionController
    joint: foot_motor_rear_left
    pid: {p: 4.0, i: 0.001, d: 0.0023}
  j10_pc:
    type: effort_controllers/JointPositionController
    joint: motor_rear_right_shoulder
    pid: {p: 4.0, i: 0.001, d: 0.0023}
  j11_pc:
    type: effort_controllers/JointPositionController
    joint: motor_rear_right_leg
    pid: {p: 4.0, i: 0.001, d: 0.0023}
  j12_pc:
    type: effort_controllers/JointPositionController
    joint: foot_motor_rear_right
    pid: {p: 4.0, i: 0.001, d: 0.0023}

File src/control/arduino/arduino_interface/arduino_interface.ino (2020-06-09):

#include <Servo.h>

class AdvServo {
  private:
  Servo servo;
  double last_actuated;
  double error_threshold = 0.5;
  int control_range = 270;
  double wait_time = 1;
  double off = 0;
  
  public:
  double goal;
  double pos;
  double spd;
  int leg; // 0: Front Left, 1: Front Right, 2: Back Left, 3: Back Right
  int joint; // 0: Hip, 1: Shoulder, 2: Wrist
  void init(int servo_pin, double starting_angle, double off);
  void setType(int tempLegNum, int tempJointNum);
  void setPosition(double tempPos, double tempSpeed);
  int getPosition();
  void update_clk();
};

void AdvServo::init(int servo_pin, double starting_angle, double tempOffset) {
  servo.attach(servo_pin, 500, 2500);
  off = tempOffset;
  pos = starting_angle + off;
  servo.write((starting_angle + off) * 180 / control_range);
  delay(1000);
  last_actuated = millis();
}

void AdvServo::setType(int tempLegNum, int tempJointNum) { 
  leg = tempLegNum;
  joint = tempJointNum;
}

void AdvServo::setPosition(double tempPos, double tempSpeed) {
  tempPos = tempPos + off;
  if(tempPos > control_range) {
//    Serial.println("Attempted to set position out of control range. Capped at max.");
    tempPos = control_range;
  }

  if(tempPos < 0) {
//    Serial.println("Attempted to set position out of control range. Capped at min.");
    tempPos = 0;
  }
  
  goal = tempPos;
  spd = tempSpeed;
}

int AdvServo::getPosition() {
  return static_cast<int>(pos - off);
}

void AdvServo::update_clk() {
  if(millis() - last_actuated > wait_time){
    if(abs(pos - goal) > error_threshold) {
      int dir = 0;
      if(goal - pos > 0) {
        dir = 1;
      } else if(goal - pos < 0) {
        dir = -1;
      }
      pos += dir * wait_time / 1000 * spd;
      servo.write(pos * 180 / control_range);
      last_actuated = millis();
    }
  }
}

String serialResponse = "";
char sz[] = "FL,H,999.9,999.9"; // general structure with max numbers allowed.
bool ESTOPPED = false;


void upper(char* s) {
  for(int i = 0; i < strlen(s); i++){
    s[i] = toupper(s[i]);
  }
}


AdvServo BR_Hip, BR_Shoulder, BR_Wrist, BL_Hip, BL_Shoulder, BL_Wrist, FR_Hip, FR_Shoulder, FR_Wrist, FL_Hip, FL_Shoulder, FL_Wrist;

void update_servos(){
  // HIPS
  FL_Hip.update_clk();
  FR_Hip.update_clk();
  BR_Hip.update_clk();
  BL_Hip.update_clk();

  // SHOULDER
  FL_Shoulder.update_clk();
  FR_Shoulder.update_clk();
  BR_Shoulder.update_clk();
  BL_Shoulder.update_clk();

  // WRIST
  FL_Wrist.update_clk();
  FR_Wrist.update_clk();
  BR_Wrist.update_clk();
  BL_Wrist.update_clk();  
}

double angleConversion(int leg, int joint, double angle) {
  if(joint == 0){
    if(leg == 0 || leg == 1) {
      angle = -angle;
    }
    angle = angle + 135;
  }
  
  if(joint == 1) {
    if(leg == 0 || leg == 2) {
      angle = 90 + angle;
    }
    if(leg == 1 || leg == 3) {
      angle = 180 - angle;
    }
  }
  
  if(joint == 2) {
    double weird_offset = 50;
    if(leg == 0 || leg == 2) {
      angle = angle - weird_offset;
    }
    if(leg == 1 || leg == 3) {
      angle = (270 + weird_offset) - angle;
    }
  }
  return angle;
}

int inverse_angleConversion(int leg, int joint, double angle) {
  if(joint == 0){
    if (leg == 0 || leg == 1) {
      angle = 135 - angle;
    }
    if (leg == 2 || leg == 3) {
      angle = angle - 135;
    }
  }
  
  if(joint == 1) {
    if(leg == 0 || leg == 2) {
      angle = angle - 90;
    }
    if(leg == 1 || leg == 3) {
      angle = 180 - angle;
    }
  }
  
  if(joint == 2) {
    double weird_offset = 50;
    if(leg == 0 || leg == 2) {
      angle = weird_offset + angle;
    }
    if(leg == 1 || leg == 3) {
      angle = (270 + weird_offset) - angle;
    }
  }
  return angle;
}

void setLegJointIDS() {
  // HIPS
  FL_Hip.setType(0, 0);
  FR_Hip.setType(1, 0);
  BL_Hip.setType(2, 0);
  BR_Hip.setType(3, 0);

  //SHOULDERS
  FL_Shoulder.setType(0, 1);
  FR_Shoulder.setType(1, 1);
  BL_Shoulder.setType(2, 1);
  BR_Shoulder.setType(3, 1);

  //WRISTS
  FL_Wrist.setType(0, 2);
  FR_Wrist.setType(1, 2);
  BL_Wrist.setType(2, 2);
  BR_Wrist.setType(3, 2);
  
}

void setup() {
// Serial.begin(38400);
 Serial1.begin(115200); // default: 9600, 19200, 57600
 
  // HIPS
  FL_Hip.init(4, 135, 0);
  FR_Hip.init(11, 135, 0);
  BL_Hip.init(7, 135, 4);
  BR_Hip.init(8, 135, -8);

  //SHOULDERS
  FL_Shoulder.init(2, 180, 0);
  FR_Shoulder.init(13, 90, -11);
  BL_Shoulder.init(5, 180, 4);
  BR_Shoulder.init(10, 90, -4);

  //WRISTS
  FL_Wrist.init(3, 0, 0);
  FR_Wrist.init(12, 270, 0);
  BL_Wrist.init(6, 0, 0);
  BR_Wrist.init(9, 270, 0);

  setLegJointIDS();
}

int loopIndex = 0;

String getPositions() {
  String temp = "";
  String delimiter = ";";

  // HIPS
//  temp = temp + String(inverse_angleConversion(FL_Hip.leg, FL_Hip.joint, FL_Hip.getPosition())) + delimiter;
//  temp = temp + String(inverse_angleConversion(FR_Hip.leg, FR_Hip.joint, FR_Hip.getPosition())) + delimiter;
//  temp = temp + String(inverse_angleConversion(BL_Hip.leg, BL_Hip.joint, BL_Hip.getPosition())) + delimiter;
//  temp = temp + String(inverse_angleConversion(BR_Hip.leg, BR_Hip.joint, BR_Hip.getPosition())) + delimiter;

  // SHOULDERS
//  temp = temp + String(inverse_angleConversion(FL_Shoulder.leg, FL_Shoulder.joint, FL_Shoulder.getPosition())) + delimiter;
//  temp = temp + String(inverse_angleConversion(FR_Shoulder.leg, FR_Shoulder.joint, FR_Shoulder.getPosition())) + delimiter;
//  temp = temp + String(inverse_angleConversion(BL_Shoulder.leg, BL_Shoulder.joint, BL_Shoulder.getPosition())) + delimiter;
//  temp = temp + String(inverse_angleConversion(BR_Shoulder.leg, BR_Shoulder.joint, BR_Shoulder.getPosition())) + delimiter;
//
  // WRISTS
  temp = temp + String(inverse_angleConversion(FL_Wrist.leg, FL_Wrist.joint, FL_Wrist.getPosition())) + delimiter;
  temp = temp + String(inverse_angleConversion(FR_Wrist.leg, FR_Wrist.joint, FR_Wrist.getPosition())) + delimiter;
  temp = temp + String(inverse_angleConversion(BL_Wrist.leg, BL_Wrist.joint, BL_Wrist.getPosition())) + delimiter;
  temp = temp + String(inverse_angleConversion(BR_Wrist.leg, BR_Wrist.joint, BR_Wrist.getPosition())) + delimiter;

  return temp;
  
}

void loop() {
//  Serial1.println("01,02,03,04,05,06,07,08,09,10,11,12"); // sends current servo positions back to RPi for speed interpolation (aka smooth linear movements)
  if(!ESTOPPED){
    update_servos();
  }
  if (Serial1.available()) {
    serialResponse = Serial1.readStringUntil('\r\n');
    // Convert from String Object to String.
    char buf[sizeof(sz)];
    serialResponse.toCharArray(buf, sizeof(buf));
    char *p = buf;
    char *str;
    int index = 0;
    int leg = -1; //0=FL, 1=FR, 2=BL, 3=BR
    int joint = -1; //0=Hip, 1=Shoulder, 2=Wrist
    double angle = -1;
    double spd = -1;
    while ((str = strtok_r(p, ",", &p)) != NULL) { // delimiter is the dash
      if(strcmp(str, "e") == 0 || strcmp(str, "E") == 0) {
        ESTOPPED = true;
//        Serial.println("ESTOPPED! Restart to resume.");
      }
      if(index == 0) {
        upper(str);
        if(strcmp(str, "FL") == 0){
          leg = 0;
        }
        if(strcmp(str, "FR") == 0){
          leg = 1;
        }
        if(strcmp(str, "BL") == 0){
          leg = 2;
        }
        if(strcmp(str, "BR") == 0){
          leg = 3;
        }
      }

      if(index == 1) {
        upper(str);
        if(strcmp(str, "H") == 0){
          joint = 0;
        }
        if(strcmp(str, "S") == 0){
          joint = 1;
        }
        if(strcmp(str, "W") == 0){
          joint = 2;
        }
      }

      if(index == 2) {
        angle = atof(str);
      }

      if(index == 3) {
        spd = atof(str);
      }
      index++;
    }

    //ERROR CHECK
    if(leg == -1 || joint == -1 || angle == -1 || spd == -1){
//      Serial.println("BIG ERROR -- INCOMPLETE DATA");
    }
    angle = angleConversion(leg, joint, angle);
    
    if(leg == 0) {
      if(joint == 0) {
        FL_Hip.setPosition(angle, spd);
      }
      if(joint == 1) {
        FL_Shoulder.setPosition(angle, spd);
      }
      if(joint == 2) {
        FL_Wrist.setPosition(angle, spd);
      }
    }

    if(leg == 1) {
      if(joint == 0) {
        FR_Hip.setPosition(angle, spd);
      }
      if(joint == 1) {
        FR_Shoulder.setPosition(angle, spd);
      }
      if(joint == 2) {
        FR_Wrist.setPosition(angle, spd);
      }
    }

    if(leg == 2) {
      if(joint == 0) {
        BL_Hip.setPosition(angle, spd);
      }
      if(joint == 1) {
        BL_Shoulder.setPosition(angle, spd);
      }
      if(joint == 2) {
        BL_Wrist.setPosition(angle, spd);
      }
    }

    if(leg == 3) {
      if(joint == 0) {
        BR_Hip.setPosition(angle, spd);
      }
      if(joint == 1) {
        BR_Shoulder.setPosition(angle, spd);
      }
      if(joint == 2) {
        BR_Wrist.setPosition(angle, spd);
      }
    }
    
  }
}

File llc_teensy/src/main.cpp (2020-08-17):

#include <Arduino.h>
#include "AdvServo.h"
#include "FootSensor.h"
#include "InverseKinematics.h"
#include "Util.h"
#include <Servo.h>
#include <ros.h>
// TODO: Include the message header file

using namespace std;

String serialResponse = "";
char msg0[] = "0,-999.9,-999.9,-999.9"; // general structure for normal position command
char msg1[] = "0,-999.9,-999.9,-999.9,-999.9,-999.9,-999.9"; // general structure for normal position/speed command
bool ESTOPPED = false;
int max_speed = 500; // deg / sec

ros::NodeHandle nh;
AdvServo BR_Hip, BR_Shoulder, BR_Wrist, BL_Hip, BL_Shoulder, BL_Wrist, FR_Hip, FR_Shoulder, FR_Wrist, FL_Hip, FL_Shoulder, FL_Wrist;
FootSensor FL_sensor, FR_sensor, BL_sensor, BR_sensor;
AdvServo * hips[4] = {&FL_Hip, &FR_Hip, &BL_Hip, &BR_Hip};
AdvServo * shoulders[4] = {&FL_Shoulder, &FR_Shoulder, &BL_Shoulder, &BR_Shoulder};
AdvServo * wrists[4] = {&FL_Wrist, &FR_Wrist, &BL_Wrist, &BR_Wrist};
Util util;
InverseKinematics ik;

void detach_servos() {
  // HIPS
  FL_Hip.detach();
  FR_Hip.detach();
  BR_Hip.detach();
  BL_Hip.detach();

  // SHOULDER
  FL_Shoulder.detach();
  FR_Shoulder.detach();
  BR_Shoulder.detach();
  BL_Shoulder.detach();

  // WRIST
  FL_Wrist.detach();
  FR_Wrist.detach();
  BR_Wrist.detach();
  BL_Wrist.detach();
}

void update_servos(){
  // HIPS
  FL_Hip.update_clk();
  FR_Hip.update_clk();
  BR_Hip.update_clk();
  BL_Hip.update_clk();

  // SHOULDER
  FL_Shoulder.update_clk();
  FR_Shoulder.update_clk();
  BR_Shoulder.update_clk();
  BL_Shoulder.update_clk();

  // WRIST
  FL_Wrist.update_clk();
  FR_Wrist.update_clk();
  BR_Wrist.update_clk();
  BL_Wrist.update_clk();
}

void update_sensors() {
  FL_sensor.update_clk();
  FR_sensor.update_clk();
  BL_sensor.update_clk();
  BR_sensor.update_clk();
}

void setLegJointIDS() {
  // HIPS
  FL_Hip.setType(0, 0);
  FR_Hip.setType(1, 0);
  BL_Hip.setType(2, 0);
  BR_Hip.setType(3, 0);

  //SHOULDERS
  FL_Shoulder.setType(0, 1);
  FR_Shoulder.setType(1, 1);
  BL_Shoulder.setType(2, 1);
  BR_Shoulder.setType(3, 1);

  //WRISTS
  FL_Wrist.setType(0, 2);
  FR_Wrist.setType(1, 2);
  BL_Wrist.setType(2, 2);
  BR_Wrist.setType(3, 2);

}

void callback( const pose_msg::LegPoses& leg_poses){
  Serial.println("complete message");
  double *p;
  p = ik.run(leg, x, y, z);

  double temp_hip = util.toDegrees(*p);

  if(leg == 1 || leg == 2){
    temp_hip *= -1;
  }
  
  double hip_angle = util.angleConversion(leg, 0, temp_hip);
  double shoulder_angle = util.angleConversion(leg, 1, util.toDegrees(*(p+1)));
  double wrist_angle = util.angleConversion(leg, 2, util.toDegrees(*(p+2)));
  
  double h_dist = abs(hip_angle - (*hips[leg]).getPosition());
  double s_dist = abs(shoulder_angle - (*shoulders[leg]).getPosition());
  double w_dist = abs(wrist_angle - (*wrists[leg]).getPosition());

  double scaling_factor = util.max(h_dist, s_dist, w_dist);

  h_dist /= scaling_factor;
  s_dist /= scaling_factor;
  w_dist /= scaling_factor;

  (*hips[leg]).setPosition(hip_angle, max_speed * h_dist);
  (*shoulders[leg]).setPosition(shoulder_angle, max_speed * s_dist);
  (*wrists[leg]).setPosition(wrist_angle, max_speed * w_dist);
}


ros::Subscriber<pose_msg::LegPoses> sub("leg_poses", &callback);

void setup() {
  ik.init(8.7, 59, 107, 130); // hip offset 0, hip_offset 1, shoulder length, wrist length

  // HIPS
  FL_Hip.init(4, 135, -2);
  FR_Hip.init(11, 135, 0);
  BL_Hip.init(7, 135, 0);
  BR_Hip.init(8, 135, -3);

  //SHOULDERS
  FL_Shoulder.init(2, 180, -3);
  FR_Shoulder.init(13, 90, -14);
  BL_Shoulder.init(5, 180, 5); // +
  BR_Shoulder.init(10, 90, 0); // -

  //WRISTS
  FL_Wrist.init(3, 0, 2);
  FR_Wrist.init(12, 270, -2);
  BL_Wrist.init(6, 0, 2);
  BR_Wrist.init(9, 270, -1);

  FL_sensor.init(A9, 17);
  FR_sensor.init(A8, 16);
  BL_sensor.init(A7, 15);
  BR_sensor.init(A6, 14);

  setLegJointIDS();

  delay(1000);

  nh.initNode();
  nh.subscribe(sub);
}

void loop() {
  nh.spinOnce();
  if(!ESTOPPED){
    update_servos();
  } else {
    detach_servos();
  }
  update_sensors();
}

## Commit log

2020-05-16 Changed to mm + calibrated offsets
2020-05-19 Yaw Implementation
2020-06-02 Added trajectory + stl
    [backpart.stl, foot.stl, frontpart.stl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]
2020-06-06 Added arduino interface layer
2020-06-07 Implemented Arduino Servo Controller
    TODO: add 2-way communication so that the arduino can send back sensor values.
2020-06-09 Added yaw + Increased Baud Rate
2020-06-09 Implemented low pass filter -- controller input
2020-06-09 Added Gerber Files
2020-06-10 Switched to CPP PlatformIO IDE
2020-06-16 Moved leg IK to teensy
2020-06-17 Added 3d models
    [FL_BR_Hip.step, Front_Shoulder.step, L_Cover.step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]
2020-06-17 Dir Restructure
    [FL_BR_Hip.step, Front_Shoulder.step, L_Cover.step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]
2020-06-17 Updated model
    [FL_BR_Hip.step, FL_BR_Hip_Joint.step, FL_BR_Hip_Joint.stl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]
2020-06-17 Updated files
    [Left_Cover.step, Left_Cover.stl]
2020-06-17 Added LED to wrist
    [Left_Wrist.step, Left_Wrist.stl]
2020-06-18 Added Foot Sensor Cabling
    [Left_Upper_Arm.step, Left_Upper_Arm.stl, Left_Wrist.step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]
2020-06-18 Added arduino lib files
2020-06-18 Added Shoulder
    [Inner_Shoulder.step, Inner_Shoulder.stl, Outer_Shoulder_Plate.step]
2020-06-19 Updated nut holes & bearings
    [FL_BR_Hip_Joint.step, Left_Cover.step, Left_Cover.stl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]
2020-06-20 Updated nut hole sizes
    [FL_BR_Hip_Joint.step, Left_Cover.step, Left_Cover.stl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]
2020-06-20 Removed bearing limit from hip assembly
    [Inner_Shoulder.step, Inner_Shoulder.stl, Outer_Shoulder_Plate.step]
2020-06-21 Added sensor-compatible board
2020-06-23 Fixed LLC_Interface + adjusted limb lengths
    [main.cpp]
2020-06-23 Updated 3D model
    [Battery_Clip.step, Battery_Clip.stl, Left_Wrist.step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]
2020-06-25 Updated Baud Rate + Added covers
    [Rear_Cover.step, Rear_Cover.stl]
2020-06-25 Updated covers
    [Front_Cover.step, Front_Cover.stl, Rear_Cover.step]
2020-06-27 Added Gait Enum + GaitParameters class
    [Bottom_Cover.step, Top_Cover.step]
2020-06-30 Implemented servo detach (for supported servos)
    [Halter_v1.stl]
2020-07-02 Implemented Foot Sensors
2020-07-09 Implemented Pitch/Roll Body IK
    [Halter_v1.stl]
2020-07-24 Quadruped Redesign
    [Adapter_Plate.step, Adapter_Plate.stl, Back_Inner_Shoulder.step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]
2020-07-24 Updated bridge
    [Bridge.step, Bridge.stl]
2020-07-26 sideplate / back inner shoulder conflict resolved
    [Back_Inner_Shoulder.step, Back_Inner_Shoulder.stl]
2020-07-26 Fixed servo covers
    [Servo Cover.stl, Servo_Cover.step, Servo_Cover.stl]
2020-07-26 Cooling vents for top cover
    [Top.step, Top.stl]
2020-07-26 Updated upper pulley
    [Upper_Pulley.step, Upper_Pulley.stl]
2020-07-28 Updated tolerances
    [Adapter_Plate.step, Adapter_Plate.stl, Electronics_Plate.step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]
2020-07-28 Fixed chamfer interference
    [Adapter_Plate.step, Adapter_Plate.stl]
2020-07-28 Added wire routing
    [Bridge.step, Bridge.stl, Left_Hip_Joint.step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]
2020-07-29 Fixed hip chamfer
    [Left_Hip_Joint.step, Right_Hip_Joint.step]
2020-08-06 Added core ROS framework.
2020-08-08 Implemented leg IK (with right offsets)
2020-08-11 Created joint angles message
2020-08-13 Updated JointAngles msg
2020-08-17 Ported URDF Model from Maurice Rahme's repo
    [Back.stl, Back_Bracket.stl, Battery.stl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]
2020-08-17 Restructured Dir for ROS
    [Adapter_Plate.step, Adapter_Plate.stl, Back.stl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]
2020-08-17 Improved URDF model dir
    [Back.stl, Back_Bracket.stl, Battery.stl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]
2020-08-17 Moved ROS pkg into catkin_ws
    [Adapter_Plate.step, Adapter_Plate.stl, Back.stl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]
2020-08-17 Renamed catkin workspace
    [Back.stl, Back_Bracket.stl, Battery.stl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]
2020-08-17 Renamed dir for clarity
    [Adapter_Plate.step, Adapter_Plate.stl, Back_Inner_Shoulder.step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]
2020-08-17 Moved 3D model + PCB files into own dir
    [Adapter_Plate.step, Adapter_Plate.stl, Back_Inner_Shoulder.step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]
2020-08-17 Major dir restructure
    [Back.stl, Back_Bracket.stl, Battery.stl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]
2020-08-17 Fixed naming standard
    [Back.stl, Back_Bracket.stl, Battery.stl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]
2020-08-17 Fixed ros conflict + Naming scheme
    [Back.stl, Back_Bracket.stl, Battery.stl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]
2020-08-20 [Sim] getting gazebo to load urdf model
    [Back.stl, Back_Bracket.stl, Battery.stl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]
2020-08-21 [sim] added gazebo motor params + control file
2020-08-22 [sim] Added joint controllers for gazebo
2020-08-22 [3dp] Adjustable Belt Tension
    [Idler_Mount.step, Idler_Mount.stl, Upper_Leg.step]
2020-08-22 [3dp] Joint Calibration
    [Hip_Calibrator.stl, L_Upper_Leg_Calibrator.stl, Lower_Leg_Calibrator.stl]
2020-12-30 LLC Subscriber Joint Angles Implemented

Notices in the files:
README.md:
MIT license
